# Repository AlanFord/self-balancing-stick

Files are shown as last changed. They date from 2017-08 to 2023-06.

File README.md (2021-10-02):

# self-balancing-stick
# UPDATE:
With apologies, this project was clearly beyond my skill set.  However, I've made a lot of progress and am closing in on completion.  Many thanks to a couple of makerspaces - [HackRVA](https://www.hackrva.org/blog/) and [BuildRVA](https://buildrva.spaces.nexudus.com/en).

The Countdown:
* 10 - Study control system theory so as to verify that replacement motors (torques, speeds, etc.) can still work. A lot has changed in this area since I last studied it 45 years ago. (**Complete**)
* 9 - Determine new control parameters using said control system theory and MATLAB (love/hate relationship right there) (**Complete**)
* 8 - Learn Arduino programming (**Complete**)
* 7 - Learn to use machine tools such that I can fabricate parts ((**Complete**)
* 6 - Pause to build a claw machine (because who doesn't want a claw machine to pick up candy and plushies?) (**Complete**)
* 5 - Make the motor clamps from ABS on an X-Carve CNC router at HackRVA (**Complete**)
* 4 - Make the balancing point from acetal on a Sherline lathe at BuildRVA (**Complete**)
* 3 - Make the gyro mount from HDPE on a Grizzly manual lathe at BuildRVA (**Complete**)
* 2 - Make the motor mount block from aluminum on a Tormach 1100 CNC mill at BuildRVA (**Complete**)
* 1 - Fabricate the reaction wheels (**In Progress!**)
* Go! (In the Near Future)

Dual Axis Reaction Wheel Inverted Pendulum

This project is inspired by an earlier project by Mike Rouleau.  For details, read [Mike.md](../master/Mike.md).

My design looks similar to Mike's, but a lot of the components required substitutes
* Motors (unavailable) replaced with Pololu brushed DC motors and hubs
* Rotors modified to mount on the hubs
* Control system parameters modified to reflect new motor constants
* Motor drivers modified to match the motors
* Unique Arduino shield designed to support two motor drivers and a connector
for the gyro

My CAD work is being done in Fusion 360.  I haven't added those files to this repository yet, but in some cases drawings (in the form of PDFs) have been included.

Design of the control system is being done in Matlab and documented in LaTeX.  The
work can be found in the folders (you guessed it) matlab and latex.

The hardware is based on what I have at hand.  
* The shaft is a 1 ft length of 3003 Aluminum tube (McMaster Carr part number 7237K33)
* 4.4:1 Metal Gearmotor 25Dx48L mm MP 12V with 48 CPR Encoder (Pololu Part # 3237)
* Pololu Universal Aluminum Mounting Hub for 4mm Shaft, #4-40 Holes (2-Pack) (Pololu Part # 1081)
* Adafruit 9-DOF Absolute Orientation IMU Fusion Breakout - BNO055 (Adafruit Part # 2472)
* Gy-521 MPU-6050 Module 3 Axis Analog Gyro and Accelerometer (various suppliers on Amazon)

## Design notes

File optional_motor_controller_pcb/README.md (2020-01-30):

# Arduino Shield for the Self-Balancing Stick

The Arduino firmware supports options for two different motor drivers - the Pololu Dual MAX14870 Motor Driver Shield (https://www.pololu.com/product/2519) and a custom shield that also uses the Maxim MAX14870 chips as motor drivers.

The Pololu motor driver shield was used in the initial testing stages to ensure the hardware and software worked together properly.  However, I found the Dupont headers to make a less-than-satisfactory connection when moving parts are involved.  Hence the move to a custom design.

The design for the Arduino shield is intended to include motor drivers for two dc motors as well as the interface for a GY-521 Gyro.

The motor drivers each use a MAX14780 motor driver IC. A barrel jack (2.1 mm, center-positive) on the shield provides power for the motors (12V, 4.2A max).  Separate pin headers are made available for connecting the motors and the GY-521 gyro.  The motors are Pololu 4.4:1 gear motors witha 48 CPR encoder, requireing a 6-pin connector.  The GY-521 interface also requires a 6-pin connector.

The Arduino pins used by each of the connectors are as follows:

GY-521 -> Arduino

* SCL -> A5/SCL
* SDA -> A4/SDA
* INT -> A3

Left Motor -> Arduino

* Vcc -> +5V
* PWM -> D7
* DIR -> D8
* Encoder_A -> D2 (Interrrupt 0)
* Encoder_B -> A2

Right Motor -> Arduino

* Vcc -> +5V
* PWM -> D12
* DIR -> D13
* Encoder_A -> D3 (Interrupt 1)
* Encoder_B -> D6

The shield contains LEDs for both motors that indicate the direction the motor is being driven.

* Red LED -> DIR=1 (Clockwise)
* Green LED -> DIR=0 (Counterclockwise)

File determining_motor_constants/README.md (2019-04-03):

# Motor Testing

## Motor Constant
Using a new/different small brushed DC motor can be aggravating.  Specs for the motor can be missing
or of questionable accuracy.  The goal here is to physically test the motors and generate any missing
motor data.

Motor testing is documented in the LaTeX report Appendices.  Normally a motor torque constant would be
measured by using the motor to drive a known load and measure the current.  In this instance an attempt to
construct a Prony Brake to use in testing the motor was unsuccessful.  Instead, a basic set of data (V, I, and rotation speed)
can be used to determine the motor constants.

The Arduino program rpm.ino is used to measure the encoder output from the motor and calculate a velocity.
The program uses the Encoder library by Paul Stoffregen (see https://www.pjrc.com/teensy/td_libs_Encoder.html).
It can be installed from the Arduino IDE (Tools -> Manage Libraries ...).  Apply a known voltage to the motor,
measure the current, and read the velocity (counts/sec) from the Arduino using the Arduino IDE serial monitor.
The encoder output must be converted from counts/sec to RPM using the encoder coefficient (counts/rev).

The folder rpm contains the Arduino program.  The spreadsheet motorConstant.xlsx is used for data
averaging when determining the average encoder output.  

## Motor/Gearbox Friction Measurement

The friction in the motor and gearbox under load was measured by varying the voltage while measuring
the current and shaft speed (using rpm.ino).  The spreadsheet motorResistance.xlsx shows the data
reduction to determine both the Coulomb and viscous friction constants.

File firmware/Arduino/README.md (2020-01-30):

# Software

This software is derived from Mike Rouleau's work and is designed for the Arduino IDE.  The following packages are required for compilation:

* I2CDevLib - see https://www.i2cdevlib.com
* PinChangeInt - see https://github.com/GreyGnome/PinChangeInt
* digitalWriteFast - see https://github.com/watterott/Arduino-Libs/tree/master/digitalWriteFast

Note that the PinChangeInt library isn't being updated and should be replaced.  DigitalWriteFast may no longer
be needed (digital writes appear to have been sped up).  I2CDevLib has several components that will be needed -
install the whole whopping thing or add parts to Arduino/library as you find you need them.

## Changes You Need to Make

There are a number of parameters in the code that may need to be altered,
depending on the hardware that you are using.  Identical changes would need to be made both in the main Controller_3.0 sketch and in the testing sketches:

* serial_Frequency (\_1_Global_Variables.ino) - The baud rate for serial communications with your computer
* encoder_PPR (\_1_Global_Variables.ino) - the number of encoder pulses per revolution of the reaction wheels.  This value is dependent on the encoder and the gearing (if any) of the motor.
* encoder_Tick_Resolution (\_1_Global_Variables.ino) - If you have a high PPR value, set this to something like 10 for noise reduction.
* gyro offsets (\_3_Setup.ino) - These will be specific to your gyro.  Specify the X Gyro Offset, the Y Gyro Offset, Z Gyro Offset, and the Z Acceleration Offset.  If you don't have these values, run the calibarateIMU sketch to measure them.
* Arduino pin definitions (main sketch file for each application) - These, located in the Controller_3.0.ino file, will depend on what motor driver you are using.  I've included to sets - chosen based on whether POLOLU or CUSTOM is defined (with a #define statement).
* Controller Feedback Variables (\_1_Global_Variables.ino) - These have names like "omega_Kp" and "theta_Kd".  They can be set via the serial link when the sketch is running, or they can be set in the global variables file.
* A Little Math (\_5_Functions.ino) - The comments at the top of the file indicate the relationship between motor orientation, motor voltage, motor shaft rotation direction, Theta, and Omega.  If your design doesn't have an identical set of relationships, use the testing sketches to determine how the relationships change.  If a positive Omega is associated with a negative ypr[1], change ypr[1] to -ypr[1] when calculating omega_Now_Unfiltered.  A similar change might be needed when calculating theta_Now_Unfiltered.  You may also need to look at \_5_Interrupts.ino to make sure the encoder directions are working correctly.

## Summary of Files:
* Controller_3.0.ino
	This is really just a dummy file intended to contain the library include files and 
	Arduino pin assignments.  The normal Arduino functions (setup and loop) are located elsewhere.

* \_1_Global_Variables.ino:
	Here we have a lot of #define statement used to define macros that will be used in the Arduino code.
	These are followed by other global variables and global volatile variables that may be changed while
	processing interrupts.

* \_3_Setup.ino:
	Here we have the traditional setup() function that would normally be found in the Controller_3.0.ino file.
	setup() includes a number of actions -
	* initializes the serial output
	* sets the pin modes for the IMU interrupt input and motor controler outputs
	* sets the pull up on the IMU interrupt pin
	* attaches functions to the IMU and encoder interrupts
	* sets the PWM wavelength (?)
	* initializes the IMU

* \_4_MainLoop.ino
	Here we have the traditional loop() function that would normally be found in the Controller_3.0.ino file.
	The loop() function is really just a container for a huge switch statement.  The switch variable (stat)
	is set from user input through the serial monitor.
```	
    Code 	Character	Function  
    127		Del 		Motors off, but print updates (?)
    121		y 		Charge left motor
    104		h 		Charge right motor
    110		n 		Charge both motors
    117		u 		Balance with left motor
    106		j 		Balance with right motor
    109		m		Balance with both motors
    122		z 		Change Zeros 
    Subcodes:
	122	z 		Set both zeros to current value	
	120	x		Set theta zeros to current value
	99	c       	Set omega zeros to current value
	111	o 		Manually set theta zero
	108	l 		Manually set omega zero

    113		q 		set theta Kp
    119		w 		set theta Ki
    101		e 		set theta Kd
    114		r 		set theta Ks
    111		o 		set theta Kt
    97		a 		set omega Kp
    115		s 		set omega Ki
    100		d 		set omega Kd
    102		f 		set omega Ks
    108		l 		set omega Kt
    116		t 		set left Target Voltage
    103		g 		set right Target Voltage
    49		1		set the angle average filter
    50		2 		set the theta zero filter
    51		3 		set the omega zero filter
    52		4 		set the angle smoothed filter
    57		9		set the friction value
    112		p 		show extended data
```

\_5_Functions.ino
	Here we have most of the basic functions.
	The functions are:
	
	get_IMU_values()
	get_left_Encoder_Speeds()
	get_right_Encoder_Speeds()
	set_left_Motor_Voltage()
	set_right_Motor_voltage()
	update_Value() (prints current and changed value to the console)
	get_Serial() (reads a new value from the console)

\_5_Interrupts.ino
	Timing is everything!  These are the functions called by the hardware interrupts.
	
	ISR_left_Encoder()
	ISR_right_Encoder()
	dmpDataReady() (processes the IMU interrupt)

\_6_Controllers.ino
	This where the magic happens!  These implement the negative feedback for control.
	They don't really "get" values, rather they are calculating updated voltages based
	on the angles and speeds.
	
	get_left_PID_Voltage_Value()
	get_right_PID_Voltage_Value()

MPU6050_6Axis_MotionApps20_mod_1.h

	MPU6050::dmpInitialize()
	MPU6050::dmpPacketAvailable()
	MPU6050::dmpGetAccel()
	MPU6050::dmpGetQuaternion()
	MPU6050::dmpGetGyro()
	MPU6050::dmpGetLinearAccel()
	MPU6050::dmpGetLinearAccelInWorld()
	MPU6050::dmpGetGravity()
	MPU6050::dmpGetEuler
	MPU6050::dmpGetYawPitchRoll()
	MPU6050::dmpProcessFIFOPacket()
	MPU6050::dmpReadAndProcessFIFOPacket()

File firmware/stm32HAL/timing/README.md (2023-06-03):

## Timing

A simple program to calculate the best I2C configuration parameters, given an I2C source clock frequency and a
required I2C speed (I2C_SPEED_FREQ_STANDARD, I2C_SPEED_FREQ_FAST,
or I2C_SPEED_FREQ_FAST_PLUS).

This code was derived from the STM32 Arduino module twi.c.

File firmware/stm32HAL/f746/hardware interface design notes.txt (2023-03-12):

The software must interface with the hardware to make all of the work together.

MCU pins used to communicate with the motors, encoders, and the imu can be determined
from the #define statements in "main.h".  While many pins are used to support peripherals
built into the NUCLEO board, the following pins are critical to this project:

Serial Port -
USART3:
	RX - Pin D8
	TX - Pin D9
	
IMU -
I2C1:
	SDA - Pin B9
	SCL - Pin B8 (Not B6!)
GPIO:
	Data Ready Interrupt - Pin F15
	
Right Motor -
TIMER1:
	PWM - Pin E9
GPIO:
	Direction - Pin E11
TIMER3:
	Encoder Channel 1 - Pin A6
	Encoder Channel 2 - Pin C7
	
Left Motor -
TIMER2:
	PWM - Pin A0
GPIO:
	Direction - Pin F14
TIMER4:
	Encoder Channel 1 - Pin D12
	Encoder Channel 2 - Pin D13
	
----------------------------------------------------
Motor and IMU Orientation

The following was extracted from the file "imu.cpp".  The sketch
represents a top-down look at the motor and imu layout.

// Discussion of IMU values and motor orientation
//
//   -----------------------------------
//   |         Left Motor/Hub          |
//   |                                 |
//   -----------------------------------
//                  |        IMU top,front      ------
//                  |         -----------       |    |
//                  |         |         |       |    |
//              --------      |  Gy-521 |       |    |
//              |      |      |         |       |    |
//              |      |      -----------       |    |
//              |      |                        |    |
//              |      |      ----------------  |    | Right Motor/Hub
//              --------      |              |  |    |
//                            |              |==|    |
//                            |              |  |    |
//                            ----------------  |    |
//                                              |    |
//                                              |    |
//                                              |    |
//                                              |    |
//                                              |    |
//                                              ------
//
//      ypr[ ] values for pitch and roll are as follows
//      Front Edge Pitch Down:  Negative Values of ypr[1]
//      Front Edge Pitch Up:    Positive Values of ypr[1]
//      Roll to the Right:      Positive Values of ypr[2]
//      Roll to the Left:       Negative Values of ypr[2]
//
//      Note that "forward" motor rotations, associated with positive voltages,
//      are alway counter-clockwise when viewed from the "shaft end", and
//      clockwise when viewed from the motor body end.
//
//      Hence,
//      Positive Right Motor rotation ==> counter-clockwise shaft spin => pitch up => positive voltage ==> positive Omega ==> positive ypr[1]
//      Positive Left Motor rotation ==> counter-clockwise shaft spin  => roll to the right => positive voltage ==> positive Theta ==> positive ypr[2]
///////////////////////////////////////////////////////////////////////////////////////////////////

------------------------------------------------------
Encoder Description

The Pololu website states that the 25D DC motors with gearboxes have an encoder with 48 counts per coil revolution.  
With a gearbox of 4.4:1, this results in 48*4.4 = 211.2 counts per shaft revolution.  This is based
on counting both the rising and falling edges of both the A and B outputs.  This is a suitable value to use
in this application because Timers 3 and 4 are configured in "TI1 and TI2" mode.

Important:  Voltage!
The Pololu encoders require a Vcc voltage of between 3.5V and 20V.  Hence, it is necessary that 
all of the encoder pins are 5V tolerant!
For the NUCLEO-F746ZG -
Function     Port/Pin        IC Pin  5V Tolerant?
L_ENC_CH1      D12             81       FT (Yes)
L_ENC_CH2      D13             82       FT (Yes)
R_ENC_CH1      A6              42       FT (Yes)
R_ENC_CH2      C7              97       FT (Yes)

------------------------------------------------------
Motor Driver Interface
Pololu Dual MAX14870 Motor Driver Shield for Arduino
https://www.pololu.com/product/2519
PWM operation up to 50 kHz
The required pins are:
DIR -> 0=forward at speed PWM %
       1=reverse at speed PWM %
PWM -> speed %

Timer Configuration:
Assume PCLK for each motor timer is 72MHz (check this for each change in MCU!!!)
Assume ARR = 255 (based on the controller code and motor voltage routines)
(PSC+1)*(ARR+1) = Fclk/Fpwm = ratio = 72MHz / 50 kHz = 1440
PSC = (ratio/(ARR+1)) -1 = (1440/256) -1 = 5.625, rounded to 6
Check:
Fpwm = Fclk/(ARR+1)/(PSC+1) = 72E6 / 256 / 7 = 40.1 kHz
______________________________________________________
IMU Interface
The IMU is a GY-521 board using a MPU-6050 module.
The required pins are:
VCC -> 3.3V/5V
GND -> GND
SCL -> B6
SDA -> B9
XDA ->
XCL ->
ADO ->
INT -> F15

The INT signal is an open-drain line that should be RISING when data is ready for download to the MCU.
The MPU-6050 can accommodate I2C frequencies of up to 400 kHz.  The original Arduino design
of this software used 100 kHz.
The I2C rise time was set at 500 nsec, based on an average value for Std (100 kHz) operation.
The I2C fall time was set to 150 nsec, based on an average value for Std (100 kHz) operation.

The GY-521 uses a 3.3V level for SCL and SDA signaling.  This is compatible with 
the STM32 NUCLEO line.

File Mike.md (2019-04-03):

## A Salute to Mike Rouleau
This project is inspired by Mike Rouleau's "Self Balancing Stick", altered so that all of the components can be fabricated at local makerspaces.  Links to descriptions of Mike Rouleau's work are:
- http://hackaday.com/2016/08/11/stick-balances-itself-with-reaction-wheels/
- https://www.youtube.com/watch?v=woCdjbsjbPg
- https://drive.google.com/file/d/0B9CxKhrEOT-3Z2Y2ajhiaWl6QU0/view
- https://drive.google.com/file/d/0B9CxKhrEOT-3ekE1MnRoT3Izdm8/view
- https://grabcad.com/library/self-balancing-stick-dual-axis-reaction-wheel-inverted-pendulum-1/details
- https://www.reddit.com/r/arduino/comments/3n0g8p/self_balancing_stick_dual_axis_reaction_wheel/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

Primary components used by Mike are:
- Mitsumi M25N-2 series Motor with a 334 PPR Encoder
- Arduino Uno Rev 3
- Seeed Studio 4A Motor Shield
- GY-521 Gyro (uses the MPU-6050 chip)

Some links to parts used by Mike:
- http://www.ebay.com/itm/171395060368?_trksid=p2060353.m1438.l2649&ssPageName=STRK%3AMEBIDX%3AIT
- http://www.mitsumi.co.jp/latest/Catalog/pdf/motorav_m25n_2_e.pdf
- http://www.ebay.com/itm/231284342156?_trksid=p2060353.m1438.l2649&ssPageName=STRK%3AMEBIDX%3AIT

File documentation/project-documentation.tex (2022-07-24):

% arara: pdflatex
% arara: nomencl
% arara: pdflatex

\documentclass[12pt,letterpaper]{article}
\usepackage{amsmath}
\usepackage[colorlinks]{hyperref} 
\usepackage[title,toc,page]{appendix}
\usepackage{graphicx}
\usepackage{caption}
\usepackage{listings}
\usepackage{titlesec}
\usepackage{todonotes}
\usepackage[intoc]{nomencl}

%% This code creates the groups
% -----------------------------------------
\usepackage{etoolbox}
\renewcommand\nomgroup[1]{%
  \item[\bfseries
  \ifstrequal{#1}{A}{Physics constants}{%
  \ifstrequal{#1}{B}{Transfer Functions}{%
  \ifstrequal{#1}{O}{Other symbols}{}}}%
]}
% -----------------------------------------

\makenomenclature

\renewcommand{\nomname}{List of Symbols}
\renewcommand{\nompreamble}{The following list describes several symbols that will be used later within the body of the document}

\newcommand{\sectionbreak}{\clearpage}

\begin{document}

\title{Oh, What a Bot!}
\author{HackRVA.org}
\date{}
\maketitle

\tableofcontents

\printnomenclature[0.5in]

\section{Introduction}
This article describes the development of a control system model for an reaction wheel pendulum, shown in Figure \ref{sketchOfPendulum}.  A reaction wheel pendulum is a variation of a simple pendulum, balanced upright, with rotating wheels
at the top in place of the pendulum bob. Each wheel is driven by a separate motor.  The pendulum is inherently unstable in the upright position - gravity will pull the pendulum over if it is not perfectly balanced.  Thus, a control system is needed to accelerate the reaction wheels, applying torques
as needed to the pendulum so as to keep it upright. The reaction wheels are mounted at right angles to each other, providing the ability to 
correct the alignment of the pendulum in any direction.

The pendulum physical structure includes a rod, an accelerometer, and two flywheels.  Each
flywheel is comprised of a motor mount, a DC brushed motor, and a reaction wheel.  The flywheel assemblies are mounted at
the top of the rod at right angles to each other and the rod.  The DC motors are wired to a motor controller and an Arduino.  The Arduino is also wired
to the accelerometer, which is located at the top of the rod.

\todo{needs a figure number}The basics of the pendulum control system is outlined in Figure \ref{fig.basicControlSystem}.  The system
can be controlled by adjusting the voltage.  An additional input F is included to describe random environmental forces that may affect the pendulum.  The random forces may result in the desired angle of the pendulum not being achieved.  More accurate control will result from feeding the resulting pendulum angle back into the control system so that the input voltage is continuously adjusted until the desired pendulum angle is achieved.  This is shown in Figure \ref{basicControl}.

In this case, however, the goal is for the pendulum to remain vertical with as little wobble as possible.
The real control comes into play when correcting for the stray forces on the system.  Hence, the control
system can be reformulated as shown in Figure \ref{fig.regulatorControlSystem}, commonly known as
a Regulator Problem.  This structure emphasizes the environmental forces as the primary input into the
system and that the feedback is primarily intended to compensate for those forces.\todo{Figure 3 is missing a feedback arrow}

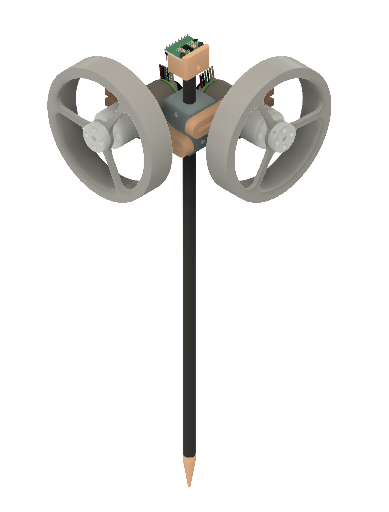
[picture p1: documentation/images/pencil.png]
 
    \captionof{figure}{Sketch of the Pendulum}  
    \label{sketchOfPendulum}
   

    \captionof{figure}{Simplified Pendulum Model}
    \label{basicControl}


    \captionof{figure}{Regulator Model}
    \label{fig.regulatorControlSystem}

\section{Pendulum Dynamics}

More detail can be added to the regulator control system description by building a mathematical model of the the
pendulum.
Figure \ref{modelOfPendulum} shows a simplified sketch of the inverted pendulum.
Reference \cite{reactionWheel} contains a summary of the model dynamics for the balancing pencil.  
The model dynamics can be summarized as
%
\begin{equation}
    m g l \sin \theta + F - I_{c}\ddot{\theta}  = I_{f}\ddot{\phi}
\end{equation}
%

\nomenclature[O]{\(m\)}{total mass of inverted pendulum (kg)}
\nomenclature[A]{\(g\)}{Gravitational constant (m s\textsuperscript{-2})}
\nomenclature[O]{\(l\)}{distance from the pivot point to the center of pendulum mass (m)}
\nomenclature[O]{\(\theta\)}{pendulum angle (rad)}
\nomenclature[O]{\(F\)}{environmental forces on the pendulum}
\nomenclature[O]{\(I_{c}\)}{moment of inertia of the pendulum (kg m\textsuperscript{2})}
\nomenclature[O]{\(I_{f}\)}{moment of inertia of the reaction wheel (kg m\textsuperscript{2})}
\nomenclature[O]{\(\phi\)}{flywheel angle (rad)}

Other references may have alternate formulations using different definitions for $\theta$ and $\phi$.\footnote{Reference \cite{monograph} has a slightly different formulation for the model dynamics; 
the sign of the gravitational term is positive rather than negative.  This difference is caused 
by Reference \cite{monograph} defining the angle from the downward, resting position
while Reference \cite{reactionWheel} defines the angle from the vertical.  
The cosines of angles differing by $\pi$ have opposite signs.}\\

After linearizing the equation by noting that $\sin{\theta} \approx \theta$ for small angles, 
the transfer function for the pendulum is then
%
\begin{equation}
    m \,g \,l \theta + F - I_{c}\ddot{\theta}  = I_{f}\ddot{\phi}
\end{equation}
%
The reaction wheel can be continuously revolving, making the reaction wheel angle $\phi$ less useful as a control parameter.
In its place we will use $\omega = \dot{\phi}$.
%
\begin{equation}
    m \,g \,l \theta + F - I_{c}\ddot{\theta}  = I_{f}\dot{\omega}\label{bigOne}
\end{equation}
%
For ease of use in later analysis, it is beneficial to split \eqref{bigOne} into two parts:
%
\begin{equation}
    m \,g \,l \theta + x(t)   = I_{c}\ddot{\theta}\label{eq.pendulum}
\end{equation}
%
\begin{equation}
    x(t) = F - I_{f}\dot{\omega}\label{eq.oddOne}
\end{equation}
%
\nomenclature[O]{\(x\)}{net torque applied to the pendulum (N m)}
where $x(t)$ is the net torque applied to the pendulum.  The sign convention is important; a positive torque $x(t)$
will accelerate the pendulum in the direction of the positive pendulum angle.  However, the sign convention in 
\eqref{eq.oddOne} indicates that  a positive acceleration of the rotor will result in a \textit{negative} acceleration of the pendulum.

Note that if the pendulum is not vertical (i.e. $\theta = 0$) gravity will begin to pull the pendulum over.  Correcting this requires accelerating the flywheel to apply torque to the pendulum.  A flywheel turning at a constant velocity applies no torque to the pendulum and will not alter the movement of the pendulum.

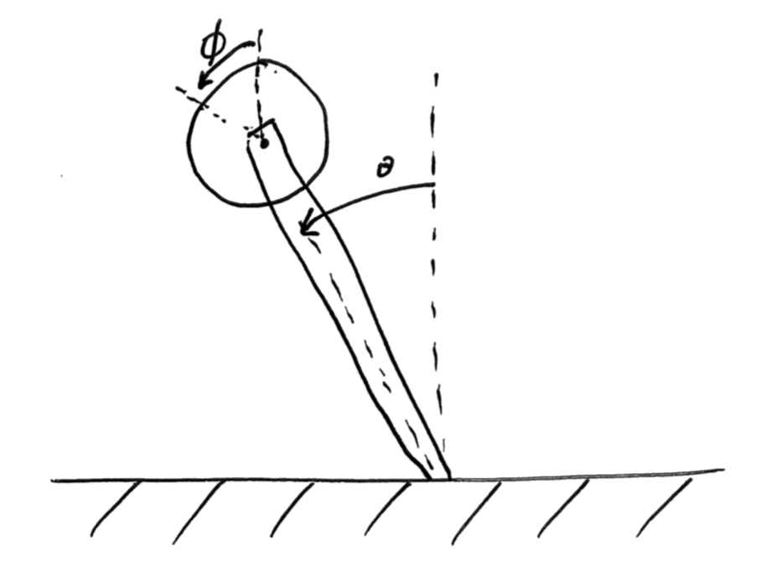
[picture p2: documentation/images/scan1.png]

    \captionof{figure}{Simplified Pendulum Model}
    \label{modelOfPendulum}

\section{Motor and Flywheel Dynamics}

Reference \cite{reactionWheel} models the motor as 
%
\begin{equation}
    I_{f} \, \ddot{\phi} \, \eta_{m} \, \eta_{g}  = K_{t} \, i
\end{equation}
%

\nomenclature[O]{\(\eta_{m}\)}{motor efficiency}
\nomenclature[O]{\(\eta_{g}\)}{gear efficiency}
\nomenclature[O]{\(K_{t}\)}{motor torque constant (N m A\textsuperscript{-1})}
\nomenclature[O]{\(i\)}{motor current (A)}

This formulation appears to have problems, as a reduction in the motor and gear efficiencies results in a 
greater flywheel acceleration for a given motor current.  Similarly, a gear ratio above unity would 
decrease the flywheel acceleration for a specified motor current/torque, which is non-physical.  The equation can be altered
to correct these issues, resulting in the following:
%
\begin{equation}
	I_{f} \, \ddot{\phi} = \, \eta_{m} \, \eta_{g} K_{t} \, i
\end{equation}
%
However, this format may not be the easiest to implement, as the motor and gear efficiencies are not known.  Reference \cite{monograph}
takes a different approach,\footnote{Note that there is no term in \eqref{simpleShaft} that represents torque associated
with external work done by the shaft.  Hence this formulation is limited to flywheels that are reasonably aerodynamic (e.g. not something that
acts as a propeller).}
%
\begin{equation}
    I_{f} \, \ddot{\phi} = T_{shaft}\label{simpleShaft}
\end{equation}
%
Where the earlier format dealt with motor/gear efficiencies using $\eta_{m}$ and $\eta_{g}$, Reference \cite{monograph} develops a correlation of friction in terms of torque required to maintain a given $\dot{\phi}$.  Here the torque will be
reformulated as 
%
\begin{equation}
    T_{shaft} = T - T_{friction}
\end{equation}
%
\begin{equation}
    T_{friction} = A \, sgn(\dot{\phi} - \dot{\theta} ) + B (\dot{\phi} - \dot{\theta})
\end{equation}
%
\begin{equation}
    T = K_{t} \, i
\end{equation}
%

\nomenclature[O]{\(T\)}{total motor torque (N m)}
\nomenclature[O]{\(T_{shaft}\)}{torque available to the flywheel (N m)}
\nomenclature[O]{\(T_{friction}\)}{torque lost to motor and gear friction (N m)}
\nomenclature[O]{\(A\)}{coulomb friction coefficient (N m)}
\nomenclature[O]{\(B\)}{rotational friction coefficient(N m rad\textsuperscript{-1} s)}

Note the use of $(\dot{\phi} - \dot{\theta})$.  Friction is dependent on the relative motion of the motor armature and the motor frame.  If the pendulum angular velocity $\dot{\phi}$ is equal to the reaction wheel angular velocity $\dot{\theta}$ there will be no relative motion between the motor armature and frame; no friction will occur.

Combining equations,
%
\begin{equation}
    I_{f} \, \ddot{\phi}  = K_{t} \, i - A \, sgn(\dot{\phi} - \dot{\theta} ) - B (\dot{\phi} - \dot{\theta})
\end{equation}
%
Again, using the notation $\omega = \dot{\phi}$,
%
\begin{equation}
    I_{f} \, \dot{\omega}  = K_{t} \, i - A \, sgn(\omega - \dot{\theta}) - B (\omega - \dot{\theta}) \label{wheel}
\end{equation}
%

As will be seen, this equation is easier to implement because $K_{t}$, $A$, and $B$ can be measured experimentally (see Appendix \ref{appendix:measure}).  

\section{Motor Control}
The previous chapter determined the relationship between the motor current and the acceleration of the flywheel.  
However, the motor will be not be controlled via motor current.  Instead, a motor controller will be used to control the 
motor by adjusting the motor voltage via a PWM signal.  The equivalent, average voltage will then regulate the motor.  
Following Reference \cite{monograph}, but recognizing the motor is at the end of a pendulum, the relationship between motor current and voltage is
%
\begin{equation}
    L\, \frac{di}{dt} + r \,i = v - K_{v} \, (\omega - \dot{\theta})
\end{equation}
%

\nomenclature[O]{\(L\)}{armature inductance (H)}
\nomenclature[O]{\(r\)}{armature resistance ($\Omega$)}
\nomenclature[O]{\(v\)}{voltage supplied to the motor (V) }
\nomenclature[O]{\(K_{v}\)}{motor voltage constant (V rad\textsuperscript{-1} s)}
\nomenclature[O]{\(\omega\)}{motor rotation speed (rad s\textsuperscript{-1})}

Normally the inductance of the motor is much lower than the resistance, such that $L/r \sim 0.001$ sec.  
In such cases it is acceptable to ignore the time dependence of the current and write
%
\begin{equation}
    r \,i = v - K_{v} \, (\omega - \dot{\theta}) \label{motor}
\end{equation}
%

Solving for i:
%
\begin{equation}
    i = \frac{v}{r} - \frac{K_{v} \, (\omega - \dot{\theta})}{r}
\end{equation}
%
Combining with \eqref{wheel}
%
\begin{equation}
    I_{f} \, \dot{\omega}  =  K_{t} \, \left( \frac{v}{r} - \frac{ K_{v} \, (\omega - \dot{\theta})}{r} \right) - A \, sgn(\omega - \dot{\theta} ) - B (\omega - \dot{\theta})
\end{equation}
Rearranging,

\begin{equation}
    I_{f} \, \dot{\omega} + \left( B+\frac{K_{t} K_{v}}{r} \right) (\omega - \dot{\theta}) +A \, sgn(\omega - \dot{\theta})= \left(\frac{K_{t}} {r}\right)v \label{eq.motorSemiFinal}
\end{equation}

Not all of the voltage results in acceleration of the reaction wheel.  As the reaction wheel velocity increases, an
increasing amount of the voltage (and the resulting torque) is consumed by friction and the back EMF.\\

The voltage used to drive the motor is determined by the controller.  Here the voltage will be set to the output of the controller
\begin{equation}
    v = u 
\end{equation}
\nomenclature[O]{\(u\)}{controller output}
Substituting into \eqref{eq.motorSemiFinal}
\begin{equation}
    I_{f} \, \dot{\omega} + \left( B+\frac{K_{v} K_{t}}{r} \right) (\omega - \dot{\theta}) +A \, sgn(\omega - \dot{\theta}) = \left(\frac{K_{t}} {r}\right)u\
\end{equation}
The simple substitution of $u$ for $v$ does not seem to have much purpose at this point in the analysis, but will be useful
when complex controllers are evaluated.\\

It is useful to assume that the control function can adjust the demand voltage by adding or subtracting a constant, depending on the current spin direction of the reaction wheel.  This means that $-A\,sgn(\dot{\phi})$ is folded
into $u$ for the purposes of this analysis.  Our motor control equation is then
\begin{equation}
    I_{f} \, \dot{\omega} + \left( B+\frac{K_{v} K_{v}}{r} \right) (\omega - \dot{\theta}) = \left(\frac{K_{t}} {r}\right)u\label{eq.motorFinal} 
\end{equation}

\section{Modeling in the Frequency Domain}
\label{sec:Modeling}

The primary objectives of a control system for the pendulum should be to stabilize the upright position of the pendulum and recovering from external forces on the pendulum.  In addition, the control system should be designed to deal with a number
of physical limitations of the physical components of the pendulum.  Specifically,
\begin{itemize}
    \item the motor voltage is limited to maximum value,
    \item the rotor velocity has a practical upper limit.
\end{itemize}

The stability of the system shown in Figure  \ref{fig.regulatorControlSystem} can be evaluated by examining the
open loop transfer function
\begin{equation}
    T(s) = P(s) C(s) M(s) R(s)
\end{equation}

\nomenclature[B]{\(P(s)\)}{pendulum transfer function}
\nomenclature[B]{\(C(s)\)}{control function}
\nomenclature[B]{\(M(s)\)}{motor transfer function}
\nomenclature[B]{\(R(s)\)}{rotor transfer function}
\nomenclature[B]{\(T(s)\)}{open loop transfer function}

The control system in terms of these transfer functions is shown in Figure \ref{transferFunction}.\\

The controller, at this point in the analysis, is assumed to be a pass-through, or
%
\begin{equation}
u = \theta
\end{equation}
Hence, the controller transfer function is
\begin{equation}
C(s) = \frac{u(s)}{\theta(s)} = 1
    \label{EQ.simpleController}
\end{equation}

The pendulum transfer function can be derived from \eqref{eq.pendulum}
%
\begin{equation}
    m \,g \,l \theta(s) + x(s) = I_{c}\theta(s) s^{2}
\end{equation}

Ignoring the environmental forces, the pendulum transfer function is 
\begin{equation}
    P(s) = \frac{\theta(s)}{x(s)}= \frac{1}{I_{c} s^{2} - m g l }
    \label{franco}
\end{equation}
%
The rotor transfer function can be derived from \eqref{eq.oddOne} by noting that the torque generated by the flywheel is
\begin{equation}
    x(s) = F(s) - I_{f}\omega(s) s
\end{equation}
%
\begin{equation}
    R(s) = \frac{x(s)}{\omega(s)} = -I_{f} s
    \label{groucho}
\end{equation}\\

Note that the transfer function for the rotor in \eqref{groucho} is negative.  Combined with the summing
junction shown in Figure \ref{transferFunction}, this produces a negative feedback control system.\\

The motor transfer function must be derived from \eqref{eq.motorFinal}.  However,  in \eqref{eq.motorFinal} $\omega$
is a function of both $\theta$ and $u$, preventing the determination of a single-input, single-output transfer function.  One solution is to make the approximation $\omega \approx (\omega - \dot{\theta})$.  The reaction wheel may rotate at hundreds of RPM, while the pendulum is expected to deviate from vertical for only brief periods.  With this approximation 
the motor transfer function can be derived from \eqref{eq.motorFinal} as
\begin{equation}
    I_{f} \, \omega(s) s + \left( B+\frac{K_{v} K_{t}}{r} \right) \omega(s) = \left(\frac{K_{t}} {r}\right)u(s)
\end{equation}
%
\begin{equation}
    M(s) = \frac{\omega(s)}{u(s)} =  \frac{\left(\frac{K_{t}} {r}\right)}{I_{f} s + (\frac{K_{v} K_{t}}{r}+B)}
    \label{rondo}
\end{equation} 

Using \eqref{EQ.simpleController}, \eqref{franco}, \eqref{groucho}, and \eqref{rondo} results in 
%
\begin{equation}
	T(s) =\frac{-(\frac{1} {I_{c}})(\frac{K_{t}}{r})s}
	{(s^2-\frac{m g l}{I_{c}})(s+(\frac{K_{v} K_{t}}{r I_{f}}+\frac{B}{I_{f}}))}
\end{equation}

Substituting in values from the appendixes, the transfer function for the pendulum is
\begin{equation}
	T(s) =\frac{-0.1731 s}{s^3 + 3.113 s^2 -34.8 s -108.3}
\end{equation}

The numerator of the transfer function is the characteristic equation that, when factored, is
$(s-5.899) (s+5.899) (s+3.113)$.

Using the root locus technique and the open loop transfer function, Figure \ref{rootLocus} shows the
behavior of the closed loop poles as a function of feedback gain.  Note that one pole is always in the right
half of the plane, indicating that the system is unstable regardless of the magnitude of the gain. \\

The system might be stabilized by using both proportional and derivative, or PD, feedback.  The control function would be:
\begin{equation}
	u = \theta + p\dot{\theta}
\end{equation}
thus
\begin{equation}
	C(s) = 1 + p s
\end{equation}
Rearranging,
\begin{equation}
	C(s) = p\left(s+\frac{1}{p}\right)\label{pd}
\end{equation}

indicating a zero at $1/p$ and a gain of $p$.
The results are sensitive to the placement of the zero.  Placing the zero to the right of the pole at -5.8993 
eliminates any oscillation but does not remediate the pole in the right half of the plane.  Placing the zero to the left of the pole at -5.8993 results in a much faster response but can result in oscillations (Figure \ref{rootLocusPD}).  Again, the pole in the right half of the plane is not remediated. \\

One additional possibility for resolving the issue of the zero at the origin would be to implement a PID controller.
\begin{equation*}
	u(t) = \theta(t) + q\int \theta\,dt + p\dot{\theta}
\end{equation*}
then
\begin{equation}
	C(s) = 1 + \frac{q}{s} + p s
\end{equation}
Rearranging,
\begin{equation}
	C(s) = p\left(\frac{s^2+\frac{s}{p}+\frac{q}{p}}{s}\right)
\end{equation}

This controller would have two zeros that can be placed as required and a pole that would cancel
the zero at the origin.  If the zeros are placed to the left of the pole at -4.7303, then the system may stabilize.
However, in the real world the original zero may not be exactly at the origin and the poles in the left side of the axis may not be exactly where they are expected (due to nonlinearities, etc.) 
leading to a less-than robust control system. \todo{verify this}\\

Finally, it is possible to include feedback from the other monitored and controlled variable, the rotor velocity.
Unfortunately, to continue to evaluate the system using a root locus analysis, the feedback from
the rotor velocity cannot be included directly in $C(s)$, as it would introduce a second input into the transfer function.  
Instead, the definition of the motor voltage $v$ is modified to include the effect of the rotor velocity feedback
\begin{equation}
    v = u + K_{\omega}\omega
\end{equation}
\nomenclature[O]{\(K_{\omega}\)}{rotor velocity feedback gain}

where $u$ continues to represent the output of a PID controller using $\theta$ as an input and $K_{\omega}\omega$ is an additional feedback
from the rotor velocity.
%
This results in \eqref{eq.motorFinal} transforming into
\begin{equation}
    I_{f} \, \dot{\omega} + \left( B+\frac{K_{v}^2}{r} \right) \omega +A \, sgn(\omega)= \left(\frac{K_{v}} {r}\right)(u + K_{\omega}\omega)
\end{equation}
The motor transfer function is then
\begin{equation}
    I_{f} \, \omega(s) s + \left( B+\frac{K_{v}^2}{r} \right) \omega(s) = \left(\frac{K_{v}} {r}\right)(u(s)+K_{\omega} \omega(s))
\end{equation}
Rearranging terms,
\begin{equation}
    M(s) = \frac{\omega(s)}{u(s)} =  \frac{\left(\frac{K_{v}} {I_{f}r}\right)}{s + (\frac{1}{I_{f}})(\frac{K_{v}^2}{r}-\frac{K_{v} K_{\omega}}{r}+B)}
    \label{rondoMucho}
\end{equation} 

Using \eqref{pd}, \eqref{franco}, \eqref{groucho}, and \eqref{rondoMucho}, the open loop transfer function is now
\begin{equation}
	T(s) =\frac{-(\frac{Kp} {I_{c}r})(s+\frac{1}{p})s}
	{s^3 + (\frac{B r-K K_{\omega}+K^2}{I_{f}r})s^2 - (\frac{m g l}{I_{c}})s - (\frac{Br-K K_{\omega}+K^2}{I_{f}r} - \frac{m g l}{I_{c}})}\label{eq.openLoop}
\end{equation}

Figure \ref{rootLocusFull} shows the root locus with $p = 1/4.5$ and $K_{\omega} = 0.075$.  With a controller gain\footnote{The gain given here is in addition to the system gain modeled in \eqref{eq.openLoop}. } of 370 the controlling close loop poles are at -11.3, -1.33, and -1.12.\\


    \captionof{figure}{Control System Modeled as Transfer Functions}
    \label{transferFunction}

 
    \captionof{figure}{Root Locus Plot With Proportional Feedback}  
    \label{rootLocus}

 
    \captionof{figure}{Root Locus Plot With PD Feedback}  
    \label{rootLocusPD}

 
    \captionof{figure}{Root Locus Plot With PD and Rotor Velocity Feedback}  
    \label{rootLocusFull}

\section{State Space Model}

A State Space model can be constructed from equations \eqref{eq.motorSemiFinal} and \eqref{bigOne}.  The
state space variables are $\omega$, $\theta$, and $\dot{\theta}$.  The state space model
is then
\begin{equation}
\dot{x_{m}} = A_{m} x + B_{m} v
\end{equation}
where $x_{m} = (\omega, \theta, \dot{\theta})^{T}$ and

\begin{equation}
A_{m} = 
\begin{bmatrix}
-\frac{B}{I_{f}}-\frac{K_{v} K{t}}{I_{f} r} & 0 & \frac{B}{I_{f}}+\frac{K_{v} K{t}}{I_{f} r}\\
0 & 0 & 1\\
\frac{B}{I_{c}}+\frac{K_{v} K{t}}{I_{c} r} & \frac{mgl}{I_{c}} & -\frac{B}{I_{c}}-\frac{K_{v} K{t}}{I_{c} r}
\end{bmatrix}
\end{equation}

\begin{equation}
B_{m} = 
\begin{bmatrix}
\frac{K_{t}}{I_{f} r} \\
0 \\
 -\frac{K_{t}}{I_{c} r}
\end{bmatrix}
\end{equation}

However, measured sensor data from motor encoder signals are proportional to the relative velocity of the 
reaction wheel, $\omega_{r} = \omega - \dot{\theta}$.  Changing the state space variables to $x = (\omega_{r}, \theta, \dot{\theta})^{T}$ is performed using a transformation matrix $x = P x_{m}$ where
\begin{equation}
 P = 
\begin{bmatrix}
1 & 0 & -1\\
0 & 1 & 0\\
0 & 0 & 1\\
\end{bmatrix}
\end{equation}

From Reference \cite{book} the new state space model is then
\begin{equation}
\dot{x} = A x + B v
\end{equation}
\begin{equation}
y = C x + D v
\end{equation}
where $x = (\omega_{r}, \theta, \dot{\theta})^{T}$,  $y=(\omega_{r},\theta)^{T}$

\begin{equation}
A = P A_{m} P^{-1}
\end{equation}

\begin{equation}
B = P B_{m}
\end{equation}

resulting in

\begin{equation}
A = 
\begin{bmatrix}
-\frac{B}{I_{f}}-\frac{B}{I_{c}}-\frac{K_{v} K{t}}{I_{f} r}-\frac{K_{v} K{t}}{I_{c} r}  & -\frac{mgl}{I_{c}} & 0 \\
0 & 0 & 1\\
\frac{B}{I_{c}}+\frac{K_{v} K{t}}{I_{c} r} & \frac{mgl}{I_{c}} & 0
\end{bmatrix}
\end{equation}

\begin{equation}
B = 
\begin{bmatrix}
\frac{K_{t}}{I_{f} r} + \frac{K_{t}}{I_{c} r}\\
0 \\
 -\frac{K_{t}}{I_{c} r}
\end{bmatrix}
\end{equation}

\begin{equation}
C = 
\begin{bmatrix}
1 & 0 & 0 \\
0 & 1 & 0 
\end{bmatrix}
\end{equation}

\begin{equation}
D = 
\begin{bmatrix}
0  \\
0 
\end{bmatrix}
\end{equation}

\section{Implementation Details}

In \autoref{sec:Modeling} the necessary constants for the control system were developed.  However those constants
need to be adjusted for the reaction wheel pendulum.

The constants developed in \autoref{sec:Modeling} took the form
\begin{equation}
	C(s) = G(1 + \frac{q}{s} + p s)
\end{equation}
where G is the controller gain, q is the integral constant, and p is the derivative constant.  However the software requires
constants in the form of 
\begin{itemize}
    \item the proportional coefficient $K_{p}$
    \item the integral coefficient $K_{i}$
    \item the derivative coefficient $K_{d}$
    \item the rotor velocity coefficient $K_{s}$
\end{itemize}

$K_{s}$ is simply $K_{\omega}$.  To generate the other required constants, the controller equation is first restructured as
\begin{equation}
	C(s) = G + \frac{Gq}{s} + Gps
\end{equation}
From this it can be seen that $K_{i} = Gq$ and $K_{d} = Gp$.  The proportional constant requires a little more work.
Recall from \eqref{eq.openLoop} the system has a gain of $Kp/I_{c}r$.  All of these terms, with the exception of $p$ are a inherent to the hardware; p
is the derivative constant. $K_{p}$ is then
\begin{equation}
K_{p} = \frac{G} {p}
\end{equation}

Another item to note in the control system implementation is that the feedback should be \textit{positive} as shown in Figure \ref{transferFunction}.  This reflects the fact that the rotor transfer function in \eqref{groucho} is negative.  This can also be seen in Figure \ref{modelOfPendulum}, where accelerating the rotor in the direction of positive $\theta$ results in a negative change in $\phi$.\\

Finally, units matter.  This documentation was created with SI units, eliminating the need to incorporate a multitude of conversion factors.  However, software is frequently constructed in more common units, for example rotor velocity in RPM, angles in degrees, and time in milliseconds or microseconds.  Hence numerical values developed in this document may need to
be converted to other units prior to use.

\begin{thebibliography}{99}
\bibitem{monograph} Block, D. J., Astrom, K. J., and Spong, M. W. (2007).  \emph{The Reaction Wheel Pendulum}. Morgan \& Claypool Publishers.
\bibitem{reactionWheel} \href{http://www.diva-portal.se/smash/get/diva2:916271/FULLTEXT01.pdf}{Ramm, A., and Sjostedt, M. (2015). Reaction wheel balanced robot, Design and Sensor Analysis of Inverted Pendulum Robot. Technical Report, KTH Royal Institute of Technology.}
\bibitem{balanceBot} \href{https://kth.diva-portal.org/smash/get/diva2:916184/FULLTEXT01.pdf}{Hellman, H. and Sunnerman, H, (2015).  Two-Wheeled Self-Balancing Robot. Technical report, KTH Royal Institute of Technology.}
\bibitem{twoWheeled} \href{http://geoffrey.chauveau.free.fr/pendulum/reports/final_report.pdf}{Chauveau, G., Chazal, D., Nakayama, D., Olsen, E., and Palm, S., (2005).  Controlling the Reaction Wheel Pendulum.}
\bibitem{hackaday} \href{https://hackaday.com/2016/08/11/stick-balances-itself-with-reaction-wheels/}{"Stick Balances Itself With Reaction Wheels" by Gerrit Coetzee}
\bibitem{book} \href{https://eng.libretexts.org/Bookshelves/Industrial_and_Systems_Engineering/Book%3A_Introduction_to_Control_Systems_(Iqbal)/08%3A_State_Variable_Models/8.04%3A_Linear_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}{Iqbal, Kamran (2020).  \emph{Introduction to Control Systems}.}
\end{thebibliography}

\begin{appendices}

\section{Motor and Gear Set Data}

Key to much of the work so far are the constants associated with the motor and gear set, $K_{t}$, $K_{v}$, $R$, and $L$.
The following work is based on a \href{https://www.pololu.com/product/3237}{Pololu  4.4:1 metal gear motor}.  

Pololu gives the following parameters for the 4.4:1 gear motor: \\
weight = 95g \\
gear ratio = 4.4:1 \\
No-load speed @ 12V = 1700 rpm (178 rad/sec)\\
No-load current @ 12V = 0.2 A \\
Stall current @ 12V = 2.1 A \\
Stall torque @ 12V (at the gearbox shaft) = 11 oz in (0.07768 Nm)\\
Encoder frequency = 211.2 counts/rev of gearbox shaft\footnote{The encoder has a frequency of 48 counts per revolution when counting both edges of both channels. With a gear ratio of 4.4:1, the encoder frequency relative to the shaft rotation is 48*4.4 counts/rev, or 211.2 counts per shaft revolution when counting both edges of both channels.}\\

A number of the motor constants can be calculated from the published Pololu parameters.  However, it
should  be noted that, for inexpensive motors, the actual motor parameters may vary from the 
published data.  In any event, the motor constants will be calculated here and then later compared
with measured data.\\

$K_{t}$ can be calculated directly from the stall current and torque: $K_{t}$ = 0.07768 Nm /  2.1 A = 
0.0370 Nm/A.  $K_{v}$ can be set equal to $K_{t}$, or 0.0370 Vs.\\

The motor winding resistance can be determined from the rated voltage and the stall current, as no back-EMF is occurring at stall
conditions.  Thus, $R$ = 12 V / 2.1 A = 5.7 ohms.\\

Motor wiring is effected via the provided 0.1"-pitch connector.
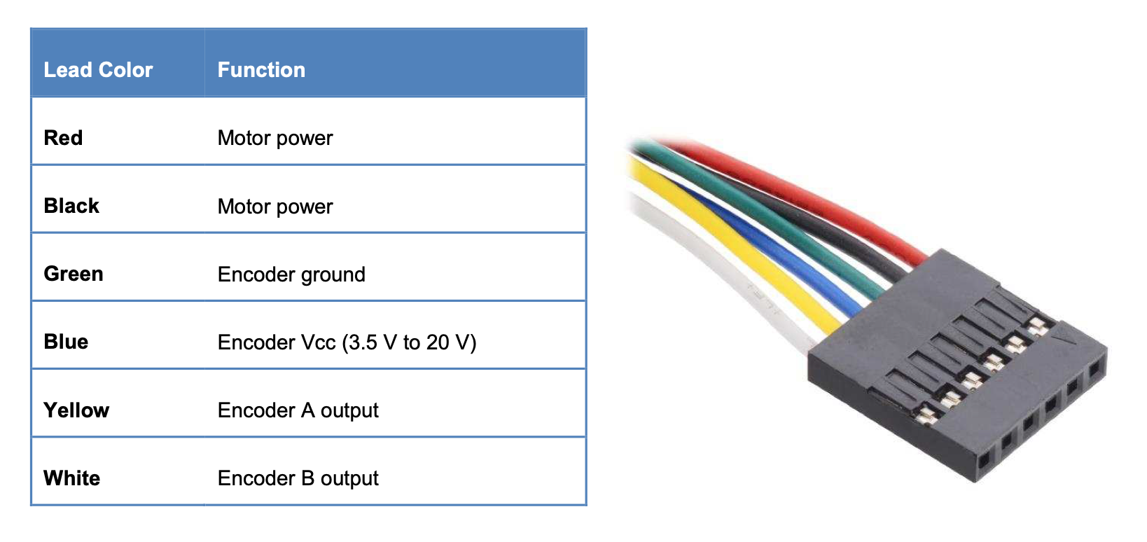
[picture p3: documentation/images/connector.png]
 

\section{Pendulum Constants}
A multitude of other values were calculated in MATLAB.\todo{needs values for both rotors and move after rotor description}  \\

\begin{tabular}{l l}
$m$ & 0.517327 kg \\
$l$ & 0.319038 m \\
$I_{c}$ & 0.046512 kg m\textsuperscript{2} \\
$I_{f}$ & 0.000168 kg m\textsuperscript{2} \\
$g$ & 9.81 m s\textsuperscript{-2} \\
\end{tabular}

\section{Measuring Motor Constants}
\label{appendix:measure}
Measurements were made to determine a number of motor constants, including $A$, $B$, $r$, $l$, and $K_{v}$, remembering that $K_{t} = K_{v}$ provided that SI units are used.\footnote{Provided SI units are used, $K_{v}$ and $K_{t}$ will have the same magnitude.  This can be seen by equating the 
mechanical and electrical power of a motor:
\begin{equation*}
    T \omega = v i
\end{equation*}
where $T$ is the motor torque.
Rearranging,
\begin{equation*}
    \frac{T}{i} = \frac{v}{\omega}
\end{equation*}
or
\begin{equation*}
    K_{t} = K_{v} 
\end{equation*}
}
Not all of these motor constants can be directly measured.  The resistance and inductance of the motor windings can be measured with an LCR meter.
Motor voltage, current, and RPM can be measured by connecting the motor to a power supply and varying the voltage.  The RPM can be measured either with a microcontroller monitoring the encoder or using a tachometer.\\

$\frac{A}{K_{t}}$ and $\frac{B}{K_{t}}$ can be determined from \eqref{wheel} by ensuring that the motor speed is constant.  Then
\begin{equation}
    i = \frac{A}{K_{t}}sgn(\omega) + \frac{B}{K_{t}} \omega
\end{equation}
Measuring $i$ at various values of $\omega$ permits estimating both $\frac{A}{K_{t}}$ and $\frac{B}{K_{t}}$ by linear
regression.  Optimally this should be performed using the rotor mounted on the motor. This ensures that
the weight of the rotor is accurately accounted for in the gearbox friction.\\

The next step is to determine values for $K_{v}$ (and hence $K_{t}$) and $R$.  Substituting \eqref{wheel} into \eqref{motor} and assuming a constant velocity we get
\begin{equation}
    v = r\frac{A}{K_{t}}sgn(\omega) + (r\frac{B}{K_{t}}+K_{v}) \omega
\end{equation}
Knowing $\frac{A}{K_{t}}$ and $\frac{B}{K_{t}}$ from the earlier regression, $r$ and $K_{v}$ can be determined by a linear regression of $v$ as a function of $\omega$.  Setting $K_{t}$ equal to $K_{v}$, values for $A$ and $B$ can then be resolved.\\

Measurements of $i$, $v$, and $\omega$ were performed with the motor driven by a 12 V power supply.  Current measurements were made with a  a $\mu$Current DVM adapter and voltage measurements were 
performed at the motor input leads.  Rotor angular velocity was measured with a hand-held tachometer.  The following table list the resulting measurements:

\begin{tabular}{|c|c|c|c|cl}
\hline
Case & $v$ & $i$ & $\omega$ & $\omega$ \\
      & (V) &  (A) & (RPM) & (rad/s) \\
\hline
1	& 0.0438	& 0.0034	& 0.	& 0. \\
2	& 0.286	& 0.015	& 0.	& 0. \\
3	& 0.601	& 0.0135	& 0.	& 0. \\
4	& 0.681	& 0.0788	& 0.	& 0. \\
5	& 1.02	& 0.0591	& 80.4	& 8.42 \\
6	& 1.487	& 0.0589	& 146.	& 15.29 \\
7	& 2.012	& 0.0599	& 230.	& 24.09 \\
8	& 2.532	& 0.0631	& 307.	& 32.15 \\
9	& 3.086	& 0.065	& 386.	& 40.42 \\
10	& 3.549	& 0.067	& 454.	& 47.54 \\
11	& 3.948	& 0.0682	& 511.	& 53.51 \\
12	& 4.56	& 0.0721	& 601.	& 62.94 \\
13	& 5.03	& 0.073	& 668.	& 69.95 \\
14	& 5.94	& 0.0751	& 807.	& 84.51 \\
15	& 6.84	& 0.0751	& 940.	& 98.44 \\
16	& 7.4	& 0.0765	& 1021.	& 106.92 \\
17	& 8.44	& 0.08	& 1175.	& 123.05 \\
18	& 9.46	& 0.082	& 1323.	& 138.54 \\
19	& 10.42	& 0.0839	& 1460.	& 152.89 \\
20	& 0.2618	& 0.0354	& 0.	& 0. \\
21	& 0.3561	& 0.0481	& 0.	& 0. \\
22	& 0.476	& 0.0646	& 0.	& 0. \\
23	& 0.597	& 0.0808	& 0.	& 0. \\
24	& 0.718	& 0.0969	& 0.	& 0. \\
25	& 0.722	& 0.0543	& 49.6	& 5.19 \\
\hline
\end{tabular}

 

 

Linear regression analysis results in the following values for the motor constants:\\
$A$ = 0.00363 N m\\
$B$ = 1.2E-5 N m/(radian/sec)\\
$r$ = 7.9 $\Omega$\\
$K_{v}$ = 0.0636 V sec\\

The coulomb friction represents approximately 5\% of the 
motor stall torque.  At the motor's no-load speed the viscous friction would double the total friction to 
approximately 7\% of the motor stall torque.  The viscous friction coefficient is significantly larger than
the value of 9.06E-7 N m/(radian/sec) measured in Reference \cite{twoWheeled}.  This may be due to
the gearbox associated with the motor used in the current work.  In any event, the friction will be included
in the system modeling.\\

$l$ was 
measured with the same instrument as 6.004 mH at 1kHz.  This gives a motor electrical time constant $l/r$ of 7.6E-4 sec.  This is the time taken by the current in the motor to go from rest to 63\% of the final steady-state current.  This
validates the assumption used in  \eqref{motor} .\\

\section{Arduino Code for Measuring RPM}

The following is an Arduino sketch can be used to monitor the speed of a dc motor in lieu of a tachometer.  The sketch is designed
to work with either an Arduino Uno or an Arduino Mega. The motor wiring described in the comments
referrs to the wiring of the Pololu 25D 4.4:1 metal gear motor.  The output is in position change 
per second, where the motor has 211.2 counts/rev of gearbox shaft. \\

\lstinputlisting{../determining_motor_constants/rpm/rpm.ino}

\section{Reaction Wheel Design Options}

The initial reaction wheel design was modeled after Reference \cite{hackaday}, with modifications to allow the reaction wheel
to mate properly with a Pololu motor hub.  The reaction wheel is shown in Figure \ref{reactionWheel}.
The reaction wheel body is Aluminum 6061 with an outer diameter of 90 mm, a width of 18 mm, and an annular thickness of 7 mm. 
Fusion 360 reports the mass of the reaction wheel to be 0.09391 kg (assuming a density of 2.7 g/cc).
The moment of inertia around the centerline is 1.562E-4 kg m\textsuperscript{2}.

An alternate, simpler design (although less elegant) is shown in Figure \ref{simpleReactionWheel}.
Fashioned from carbon steel with a density of  7.85 g/cc, the diameter of the wheel is 90 mm and the
thickness is 3.175 mm (1/8").  The reaction wheel mass is 0.175 kg and the moment of inertia 
around the centerline is 1.605E-04 kg m\textsuperscript{2}.  The simpler design with only a small change in the moment
of inertia permits an easier fabrication at a cost of a doubling of the reaction wheel mass.

A third, and final, design is less elegant still.  Figure \ref{acrylicReactionWheel} shows a reaction wheel fabricated from 3mm thick acrylic sheet, M6 button head bolts and nyloc nuts.  This design in intended to maintain a moment of inertia similar to the earlier designs, minimize the weight of the reaction wheel, and be easier to fabricate with common makerspace tools.  The wheel has an outer diameter of 90 mm with 12 bolts uniformly spaced at a radial distance of 39 mm.  The reaction wheel mass (including bolts) is  0.0808 kg, approximately half the mass of the steel reaction wheel.  The moment of inertial around the centerline (including the bolts) is 9.836E-05 kg m\textsuperscript{2}.  As with the other designs this reaction wheel is capable of being mated with a Pololu motor hub.

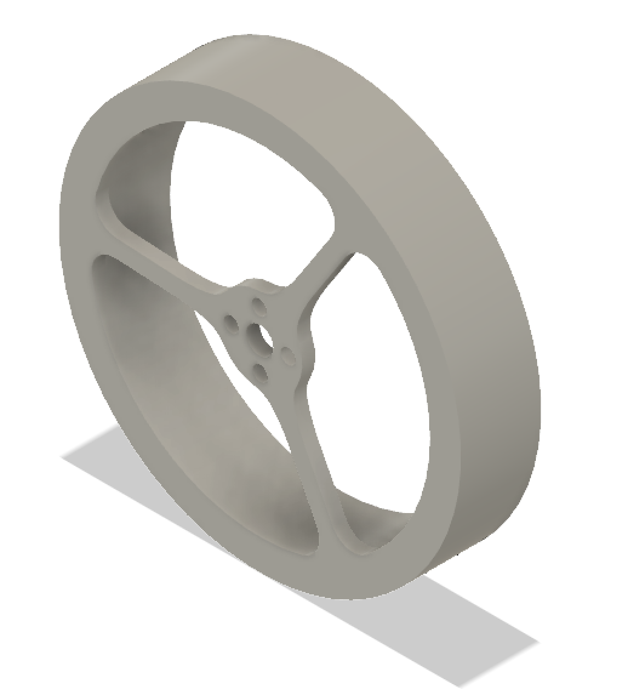
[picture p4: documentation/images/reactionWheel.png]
 
    \captionof{figure}{Aluminum Reaction Wheel}  
    \label{reactionWheel}

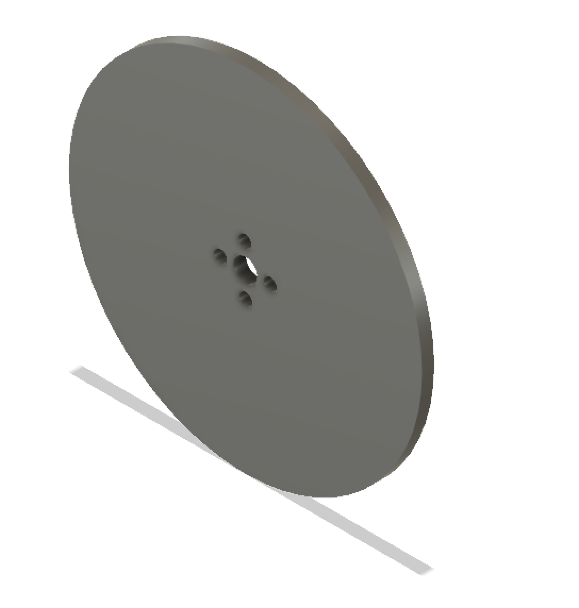
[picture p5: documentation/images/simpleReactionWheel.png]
 
    \captionof{figure}{Simplified Carbon Steel Reaction Wheel}  
    \label{simpleReactionWheel}

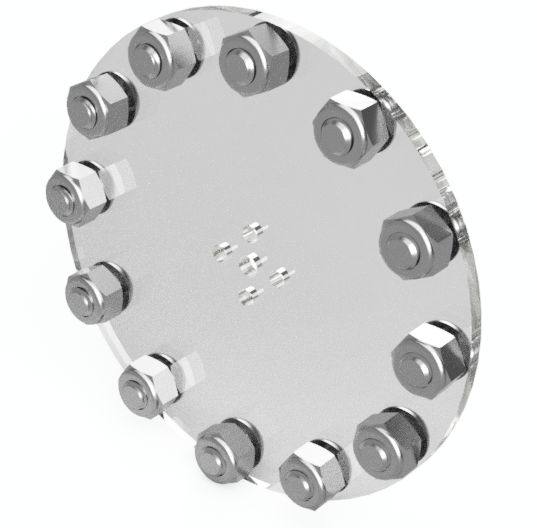
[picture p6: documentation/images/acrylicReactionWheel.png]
 
    \captionof{figure}{Simplified Acrylic Reaction Wheel}  
    \label{acrylicReactionWheel}

\end{appendices}

\end{document}

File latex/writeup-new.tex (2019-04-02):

\documentclass[12pt,letterpaper]{article}
\usepackage{amsmath}
\usepackage[colorlinks]{hyperref} 
\usepackage[title,toc,page]{appendix}
\usepackage{graphicx}
\usepackage{caption}
\usepackage{listings}
\usepackage{titlesec}
\newcommand{\sectionbreak}{\clearpage}
\begin{document}

\title{Oh, What a Bot!}
\author{HackRVA.org}
\date{}
\maketitle

\section{Introduction}
This article describes the development of a control system model for an reaction wheel pendulum, shown in Figure \ref{sketchOfPendulum}.  A reaction wheel pendulum is a variation of a simple pendulum, balanced upright, with rotating wheels
at the top in place of the pendulum bob. Each wheel is driven by a separate motor.The pendulum is inherently unstable in the upright position - gravity will pull the pendulum over if it is not perfectly balanced.  Thus, a control system is needed to accelerate the reaction wheels, applying torques
as needed to the pendulum so as to keep it upright. The reaction wheels are mounted at right angles to each other, providing the ability to 
correct the alignment of the pendulum in any direction.

The pendulum physical structure includes a rod, an accelerometer, and two flywheels.  Each
flywheel is comprised of a motor mount, a DC brushed motor, and a reaction wheel.  The flywheel assemblies are mounted at
the top of the rod at right angles to each other and the rod.  The DC motors are wired to a motor controller and an Arduino.  The Arduino is also wired
to the accelerometer, which is located at the top of the rod.

The basics of the pendulum control system is outlined in Figure \ref{fig.basicControlSystem}.  The system
can be controlled by adjusting the voltage.  An additional input F is included to describe random environmental forces that may affect the pendulum.  The random forces may result in the desired angle of the pendulum not being achieved.  More accurate control will result from feeding the resulting pendulum angle back into the control system so that the input voltage is continuously adjusted until the desired pendulum angle is achieved.  This is shown in Figure \ref{basicControl}.

In this case, however, the goal is for the pendulum to remain vertical with as little wobble as possible.
The real control comes into play when correcting for the stray forces on the system.  Hence, the control
system can be reformulated as shown in Figure \ref{fig.regulatorControlSystem}, commonly known as
a Regulator Problem.  This structure emphasizes the environmental forces as the primary input into the
system and that the feedback is primarily intended to compensate for those forces.

 
    \captionof{figure}{Sketch of the Pendulum}  
    \label{sketchOfPendulum}
   

    \captionof{figure}{Simplified Pendulum Model}
    \label{basicControl}


    \captionof{figure}{Regulator Model}
    \label{fig.regulatorControlSystem}

\section{Pendulum Dynamics}

More detail can be added to the regulator control system description by building a mathematical model of the the
pendulum.
Figure \ref{modelOfPendulum} shows a simplified sketch of the inverted pendulum.
Reference \cite{reactionWheel} contains a summary of the model dynamics for the balancing pencil.  
The model dynamics can be summarized as
%
\begin{equation}
    m g l \sin \theta + F - I_{c}\ddot{\theta}  = I_{f}\ddot{\phi}
\end{equation}
%
where: \\
$ m =$ total mass of inverted pendulum (kg)\\
$g =$ gravitational constant  (m s\textsuperscript{-2}) \\
$l =$ distance from the pivot point to the center of pendulum mass (m)\\
$\theta =$ pendulum angle (rad) \\
$F =$ environmental forces on the pendulum\\
$I_{c} =$ moment of inertia of the pendulum (kg m\textsuperscript{2}) \\
$I_{f} =$ moment of inertia of the reaction wheel (kg m\textsuperscript{2}) \\
$\phi =$ flywheel angle (rad) \\

Other references may have alternate formulations using different definitions for $\theta$ and $\phi$.\footnote{Reference \cite{monograph} has a slightly different formulation for the model dynamics; 
the sign of the gravitational term is positive rather than negative.  This difference is caused 
by Reference \cite{monograph} defining the angle from the downward, resting position
while Reference \cite{reactionWheel} defines the angle from the vertical.  
The cosines of angles differing by $\pi$ have opposite signs.}\\

After linearizing the equation by noting that $\sin{\theta} \approx \theta$ for small angles, 
the transfer function for the pendulum is then
%
\begin{equation}
    m \,g \,l \theta + F - I_{c}\ddot{\theta}  = I_{f}\ddot{\phi}
\end{equation}
%
The reaction wheel can be continuously revolving, making the reaction wheel angle, $\phi$, less useful as a control parameter.
In its place we will use $\omega = \dot{\phi}$.
%
\begin{equation}
    m \,g \,l \theta + F - I_{c}\ddot{\theta}  = I_{f}\dot{\omega}\label{bigOne}
\end{equation}
%
For ease of use in later analysis, it is beneficial to split \eqref{bigOne} into two parts:
%
\begin{equation}
    m \,g \,l \theta + u(t)   = I_{c}\ddot{\theta}\label{eq.pendulum}
\end{equation}
%
\begin{equation}
    u(t) = F - I_{f}\dot{\omega}\label{oddOne}
\end{equation}
%
where $u(t)$ is the net torque applied to the pendulum.  The sign convention is important; a positive torque $u(t)$
will accelerate the pendulum in the direction of the positive pendulum angle.  However the sign convention in 
\eqref{oddOne} indicates that  a positive acceleration of the rotor will result in a \textit{negative} acceleration of the pendulum.

Note that if the pendulum is not vertical (i.e. $\theta = 0$) gravity will begin to pull the pendulum over.  Correcting this requires accelerating the flywheel to apply torque to the pendulum.  A flywheel turning at a constant velocity applies no torque to the pendulum and will not alter the movement of the pendulum.


    \captionof{figure}{Simplified Pendulum Model}
    \label{modelOfPendulum}

\section{Motor and Flywheel Dynamics}

Reference \cite{reactionWheel} models the motor as 
%
\begin{equation}
    I_{f} \, \ddot{\phi} \, \eta_{m} \, \eta_{g}  = K_{t} \, i
\end{equation}
%
where: \\
$\eta_{m} =$ motor efficiency \\
$\eta_{g} =$ gear efficiency \\
$K_{t} =$ motor torque constant (N m A\textsuperscript{-1}) \\
$i =$ motor current \\

This formulation appears to have problems, as a reduction in the motor and gear efficiencies results in a 
greater flywheel acceleration for a given motor current.  Similarly, the gear ratio above unity would 
decrease the flywheel acceleration for a specified motor current/torque, which is non-physical.  The equation can be altered
to correct these issues, resulting in the following:
%
\begin{equation}
	I_{f} \, \ddot{\phi} = \, \eta_{m} \, \eta_{g} K_{t} \, i
\end{equation}
%
However, this format may not be the easiest to implement, as the motor and gear efficiencies are not known.  Reference \cite{monograph}
takes a different approach,
%
\begin{equation}
    I_{f} \, \ddot{\phi} = T_{shaft}
\end{equation}
%
Where the earlier format dealt with motor/gear efficiencies using $\eta_{m}$ and $\eta_{g}$, Reference \cite{monograph} develops a correlation of friction in terms of torque required to maintain a given $\dot{\phi}$.  Here the torque will be
reformulated as 
%
\begin{equation}
    T_{shaft} = T - T_{friction}
\end{equation}
%
\begin{equation}
    T_{friction} = A \, sgn(\dot{\phi} ) + B \dot{\phi} 
\end{equation}
%
\begin{equation}
    T = K_{t} \, i
\end{equation}
%
where \\
$T =$ the total motor torque \\
$T_{shaft} =$ torque available to the flywheel \\
$T_{friction} =$ torque lost to motor and gear friction \\
$A =$ coulomb friction coefficient \\
$B =$ rotational friction coefficient \\

Combining equations and adding the reduction gear ratio,
%
\begin{equation}
    I_{f} \, \ddot{\phi}  = K_{t} \, i - A \, sgn(\dot{\phi} ) - B \dot{\phi}
\end{equation}
%
Again, using the notation $\omega = \dot{\phi}$,
%
\begin{equation}
    I_{f} \, \dot{\omega}  = K_{t} \, i - A \, sgn(\omega) - B \omega \label{wheel}
\end{equation}
%

As will be seen, this equation is easier to implement because $K_{t}$, $A$, and $B$ can be measured experimentally (see Appendixes \ref{appendix:measure} and \ref{appendix:friction}).

\section{Motor Control}
The previous chapter determined the relationship between the motor current and the acceleration of the flywheel.  
However, the motor will be not be controlled via motor current.  Instead, a motor controller will be used to control the 
motor by adjusting the motor voltage via a PWM signal.  The equivalent, average voltage will then regulate the motor.  
Reference \cite{monograph} give the relationship between motor current and voltage as
%
\begin{equation}
    l \, \frac{di}{dt} + r \,i = v - K_{v} \, \omega
\end{equation}
%
where: \\
$l =$ armature inductance (henry) \\
$r =$ armature resistance (ohm) \\
$v =$ voltage supplied to the motor (volt) \\
$K_{v} =$ motor voltage constant (V  rad\textsuperscript{-1} sec) \\
$\omega =$ motor rotation speed (rad sec\textsuperscript{-1}) \\

Normally the inductance of the motor is much lower than the resistance, such that $l/r \sim 0.001$.  
In such cases it is acceptable to ignore the time dependence of the current and write
%
\begin{equation}
    r \,i = v - K_{v} \, \omega \label{motor}
\end{equation}
%
Note that, provided mks units are used, $K_{v}$ and $K_{t}$ will have the same magnitude.  This can be seen by equating the 
mechanical and electrical power
%
\begin{equation}
    T \omega = v i
\end{equation}
%
where $T =$ is the motor torque.
Rearranging,
%
\begin{equation}
    \frac{T}{i} = \frac{v}{\omega}
\end{equation}
%
or
%
\begin{equation}
    K_{t} = K_{v} 
\end{equation}
%

Back to the motor equation, we can solve \eqref{motor} for i:
%
\begin{equation}
    i = \frac{v}{r} - \frac{K_{v} \, \omega}{r}
\end{equation}
%
Combining with \eqref{wheel}
%
\begin{equation}
    I_{f} \, \dot{\omega}  =  K_{t} \, \left( \frac{v}{r} - \frac{ K_{v} \, \omega}{R} \right) - A \, sgn(\omega ) - B \omega
\end{equation}
Rearranging,

\begin{equation}
    I_{f} \, \dot{\omega} + \left( B+\frac{K_{t} K_{v}}{r} \right) \omega +A \, sgn(\omega)= \left(\frac{K_{t}} {r}\right)v 
\end{equation}

Recognizing that $K_{t} = K_{v}$ and replacing them with $K$,
\begin{equation}
    I_{f} \, \dot{\omega} + \left( B+\frac{K^2}{r} \right) \omega +A \, sgn(\omega)= \left(\frac{K} {r}\right)v\label{eq.motorFinal} 
\end{equation}

Not all of the voltage results in acceleration of the reaction wheel.  As the reaction wheel velocity increases, an
increasing amount of the voltage (and the resulting torque) is consumed by friction and the back EMF.

We will assume that the control function can adjust the demand voltage by adding or subtracting a constant, depending on the current spin direction of the reaction wheel.  This means that $-A\,sgn(\dot{\phi})$ is folded
into $v$ for the purposes of this analysis.  

\section{Modeling in the Frequency Domain}

The primary objectives of a control system for the pendulum should be to stabilize the upright position of the pendulum and recovering from external forces on the pendulum.  In addition, the control system should be design to deal with a number
of physical limitations of the physical components of the pendulum.  Specifically,
\begin{itemize}
    \item the motor voltage is limited to maximum value,
    \item The rotor velocity has a practical upper limit.
\end{itemize}

The stability of the system shown in Figure  \ref{fig.regulatorControlSystem} can be evaluated by examining the
open loop transfer function
\begin{equation}
    T(s) = P(s) C(s) M(s) R(s)
\end{equation}
where $P(s)$ is the pendulum transfer function, $C(s)$ is the control function, $M(s)$ is the motor transfer function, and $R(s)$ is the rotor transfer function.  
The control system in terms of these transfer functions is shown in Figure \ref{transferFunction}.\\

The controller, at this point in the analysis, is assumed to be a pass-through, or
%
\begin{equation}
v = \theta
\end{equation}
Hence, the controller transfer function is
\begin{equation}
C(s) = \frac{v(s)}{\theta(s)} = 1
    \label{EQ.simpleController}
\end{equation}

The pendulum transfer function can be derived from \eqref{eq.pendulum}
%
\begin{equation}
    m \,g \,l \theta(s) + u(s) = I_{c}\theta(s) s^{2}
\end{equation}

The rotor transfer function can be derived by noting that the torque generated by the flywheel is
\begin{equation}
    u(s) = F(s) - I_{f}\omega(s) s
\end{equation}
%
Ignoring the environmental forces, the pendulum transfer functions are 
\begin{equation}
    P(s) = \frac{\theta(s)}{u(s)}= \frac{1}{I_{c} s^{2} - m g l }
    \label{franco}
\end{equation}
%
\begin{equation}
    R(s) = \frac{u(s)}{\omega(s)} = -I_{f} s
    \label{groucho}
\end{equation}\\

Note that the transfer function for the rotor in \eqref{groucho} is negative.  Combined with the summing
junction shown in Figure \ref{transferFunction}, this produces a negative feedback control system.\\

From \eqref{eq.motorFinal} the transfer function for the motor is:
\begin{equation}
    I_{f} \, \omega(s) s + \left( B+\frac{K^2}{r} \right) \omega(s) = \left(\frac{K} {r}\right)v(s)
\end{equation}
\begin{equation}
    M(s) = \frac{\omega(s)}{v(s)} =  \frac{\left(\frac{K} {r}\right)}{I_{f} s + (\frac{K^2}{r}+B)}
    \label{rondo}
\end{equation} 

Using \eqref{EQ.simpleController}, \eqref{franco}, \eqref{groucho}, and \eqref{rondo} results in 
%
\begin{equation}
	T(s) =\frac{-(\frac{1} {I_{f}I_{c}})(\frac{K}{r})s}
	{(s^2-\frac{m g l}{I_{c}})(s+(\frac{K^2}{r I_{f}}+\frac{B}{I_{f}}))}
\end{equation}

Substituting in values from the appendixes, the transfer function for the pendulum is
\begin{equation}
	T(s) =\frac{-0.2464 s}{s^3 + 4.73 s^2 -34.8 s -164.6}
\end{equation}

The numerator of the transfer function is the characteristic equation that, when factored, is
$(s-5.8993) (s+5.8993) (s+4.7303)$.

Using the root locus technique and the open loop transfer function, Figure \ref{rootLocus} shows the
behavior of the closed loop poles as a function of feedback gain.  Note that one pole is always in the right
half of the plane, indicating that the system is unstable regardless of the magnitude of the gain.

One possible method of stabilizing the system would be to use both proportional and derivative, or PD, feedback.  The control function would be.
\begin{equation}
	C(s) = 1 + p s
\end{equation}
Rearranging,
\begin{equation}
	C(s) = \frac{s+\frac{1}{p}}{p}
\end{equation}

indicating a zero at $1/p$ and a gain of $1/p$.
The results are sensitive to the placement of the zero.  Placing the zero to the right of the pole at -5.8993 
eliminates any oscillation, but does not remediate the pole in the right half of the plane.  Placing the zero to the left of the pole at -5.8993 results in a much faster response, but can result in oscillations (Figure \ref{rootLocusPD}).  Again, the pole in the right half of the plane is not remediated. \\

One possibility for resolving the issue of the zero at the origin would be to implement a PID controller.
\begin{equation}
	C(s) = 1 + \frac{q}{s} + p s
\end{equation}
Rearranging,
\begin{equation}
	C(s) = \frac{ps^2+s+q}{s}
\end{equation}

This controller would have two zeros that can be placed as required and a pole that would cancel
the zero at the origin.  If the zeros are placed to the left of the pole at -4.7303, then the system may stabilize.
However, in the real world the original zero may not be exactly at the origin and the poles in the left side of the axis may not be exactly where they are expected (due to nonlinearities, etc.) 
leading to a less-than robust control system. \\

Finally, it is possible to include feedback from the other monitored and controlled variable, the rotor velocity.
Unfortunately, to continue to evaluate the system using a root locus analysis, the feedback from
the rotor velocity will have to be directly factored into the transfer function.  \\

Here we modify \eqref{motor} to include the feedback from the rotor velocity:
\begin{equation}
    r \,i = v +K_{\omega}\omega - K_{v} \, \omega \label{motorUpdated}
\end{equation}

where: \\
$ K_{\omega} =$ rotor velocity feedback gain.\\

Solving for i,
\begin{equation}
    i = \frac{v}{r} - \frac{(K-K_{\omega}) \, \omega}{r}
\end{equation}

and
\begin{equation}
    M(s) = \frac{\omega(s)}{v(s)} =  \frac{\left(\frac{K} {I_{f}r}\right)}{s + (\frac{1}{I_{f}})(\frac{K^2}{r}-\frac{K K_{\omega}}{r}+B)}
    \label{rondoMucho}
\end{equation} 

Using \eqref{EQ.simpleController}, \eqref{franco}, \eqref{groucho}, and \eqref{rondoMucho}, the open loop transfer function is now
\begin{equation}
	T(s) =\frac{-(\frac{K} {I_{c}r})s}
	{s^3 + (\frac{B r-K K_{\omega}+K^2}{I_{f}r})s^2 - (\frac{m g l}{I_{c}})s - (\frac{Br-K K_{\omega}+K^2}{I_{f}r} - \frac{m g l}{I_{c}})}
\end{equation}

Figure \ref{rootLocusFull} shows the root locus with $p = 1/4.5$ and $K_{\omega} = 0.075$.  With a system gain of 266 the controlling poles are at -11.5205, -1.5353, and -0.999.\\


    \captionof{figure}{Control System Modeled as Transfer Functions}
    \label{transferFunction}

 
    \captionof{figure}{Root Locus Plot With Proportional Feedback}  
    \label{rootLocus}

 
    \captionof{figure}{Root Locus Plot With PD Feedback}  
    \label{rootLocusPD}

 
    \captionof{figure}{Root Locus Plot With PD and Rotor Velocity Feedback}  
    \label{rootLocusFull}

\begin{thebibliography}{99}
\bibitem{monograph} Block, D. J., Astrom, K. J., and Spong, M. W. (2007).  \emph{The Reaction Wheel Pendulum} . Morgan \& Claypool Publishers.
\bibitem{reactionWheel} \href{http://www.diva-portal.se/smash/get/diva2:916271/FULLTEXT01.pdf}{Ramm, A., and Sjostedt, M. (2015). Reaction wheel balanced robot, Design and Sensor Analysis of Inverted Pendulum Robot. Technical Report, KTH Royal Institute of Technology.}
\bibitem{balanceBot} \href{https://kth.diva-portal.org/smash/get/diva2:916184/FULLTEXT01.pdf}{Hellman, H. and Sunnerman, H, (2015).  Two-Wheeled Self-Balancing Robot. Technical report, KTH Royal Institute of Technology.}
\bibitem{twoWheeled} \href{http://geoffrey.chauveau.free.fr/pendulum/reports/final_report.pdf}{Chauveau, G., Chazal, D., Nakayama, D., Olsen, E., and Palm, S., (2005).  Controlling the Reaction Wheel Pendulum.}
\end{thebibliography}

\begin{appendices}

\section{Motor and Gear Set Data}

Key to much of the work so far are the constants associated with the motor and gear set, $K_{t}$, $K_{v}$, $R$, and $L$.
Here we are using a \href{https://www.pololu.com/product/3237}{Pololu  4.4:1 metal gear motor}.  

Pololu gives the following parameters for the 4.4:1 gear motor: \\
weight = 95g \\
gear ratio = 4.4:1 \\
No-load speed @ 12V = 1700 rpm (178 rad/sec)\\
No-load current @ 12V = 0.2 A \\
Stall current @ 12V = 2.1 A \\
Stall torque @ 12V = 11 oz in (0.07768 Nm)\\
Encoder frequency = 211.2 counts/rev of gearbox shaft\\

A number of the motor constants can be calculated from the published Pololu parameters.  However, it
should  be noted that, for inexpensive motors, the actual motor parameters may vary from the 
published data.  In any event, the motor constants will be calculated here and then later compared
with measured data.

$K_{f}$ can be calculated directly from the stall current, gear ratio, and torque: $K_{f}$ = 0.07768 Nm /  2.1 A = 
0.0370 Nm/A.  $K_{v}$ can be set equal to $K_{f}$, or 0.0370 Vs.

The motor winding resistance can be determined from the rated voltage and the stall current, as no back-EMF is occurring at stall
conditions.  Thus, $R$ = 12 V / 2.1 A = 5.7 ohms.

\section{Pendulum Constants}
A multitude of other values were calculated in MATLAB.  \\

\begin{tabular}{l l}
$m$ & 0.517327 kg \\
$l$ & 0.319038 m \\
$I_{c}$ & 0.046508 kg m\textsuperscript{2} \\
$I_{f}$ & 0.000164 kg m\textsuperscript{2} \\
$g$ & 9.81 m s\textsuperscript{-2} \\
\end{tabular}

\section{Measuring Motor Constants}
\label{appendix:measure}
Measurements were made to determine a number of motor constants, including $r$, $l$, and $K_{v}$.  

$r$ was measured using an EXTEC LCR meter, on the $R_{DC}$ setting, as 5.82 $\Omega$. $l$ was 
measured with the same instrument as 5.994 mH at 1kHz.  This gives a motor electrical time constant $l/r$ of 0.001 sec.  This is the time taken by the current in the motor to go from rest to 63\% of the final steady-state current.

$K_{v}$ was measured by driving a motors with a constant voltage and
varying loads while measuring $V$, $i$, and $\omega$.  

The motor was driven with a 12 V power supply.  The current was measured by the power supply.  Measuring current in this manner can have larger uncertainties, but comparing with measurements from a $\mu$Current DVM adapter indicated that the power supply current measurement was reasonable.  

$\omega$ was measured using the motor's encoder and an Arduino.  The encoder measured the shaft speed, not the gear-set speed.  However, a conversion coefficient of 211.2 counts/revolution was used to convert the encoder pulse rate to gear set rotation speed.

The following table shows the results for three different loads.  The first load was just rotor friction.  The second load added the Pololu hub adapter.  The third load included a plastic wheel attached to a propeller to increase the drag.
The resulting measured values are as follows: \\

\begin{tabular}{|c|c|c|c|c|c|}
\hline
Case & $v$ & $i$ & speed & $\omega$ & $\omega$ \\
      & (V) &  (A) & (counts/sec) & (RPM) & (sec\textsuperscript{-1}) \\
\hline
1    & 11.95 & 0.0675 & 5,942.2   & 1,688.1   & 176.74 \\
2    & 11.95 & 0.075   & 5,923.58 & 1,682.83 & 176.19 \\ 
3    & 11.95 & 0.153   & 5,574.88 & 1583.77  & 165.82 \\
\hline
\end{tabular}

Calculating $K_{v}$ can be approached two ways.  The first is to solve \eqref{motor} using the measured
value of $R$.  The resulting values of $K_{v}$, one for each case, are:

\begin{tabular}{|c|c|}
\hline
Case & $K_{v}$  \\
         & (V sec) \\
\hline
1    & 0.0654  \\
2    & 0.0653  \\
3    & 0.0667  \\
\hline
\end{tabular}

A second approach is to use two cases in \eqref{motor} and solve simultaneously for $R$ and $K_{v}$.
Cases 1 and 3 were chosen because of the largest difference in $i$, attempting to ensure that the two
cases are independent.  This results in a values of $r$ = 8.24 $\Omega$ and $K_{v}$ = 0.0645 V sec.

The value of $K_{v}$ is fairly consistent with the values determined in the first approach, but the value
of $r$ appears to be high.  This may be caused by the limited change in $i$ in the data.  Use of a larger
load torque might result in a larger value of $i$ and a better estimate of $r$.  However, for the purposes
of this work the following values will be used:

\begin{tabular}{|c|c|c|}
\hline
r                   & $K_{v}$  & $K_{t}$ \\
($\Omega$)   & (V sec)   & (N m A) \\
\hline
5.82    & 0.0667  & 0.0667  \\
\hline
\end{tabular}

\section{Measuring Motor Friction Constants}
\label{appendix:friction}
Friction in the motor was evaluated by measuring the supply current as a function of motor speed.
The friction force is related to the motor current as $F = K_{t} i$.  The measurement was performed
by using a power supply with a variable current limit.  For various currents the speed of the motor
was measured by monitoring the motor encoder output with an Arduino.  The current was measured
both at the power supply as well as with a $\mu$Current DVM adapter.

The following data was collected:

\begin{tabular}{|c|c|c|c|c|c|}
Supply Voltage & Supply Current & $\mu$Current & Speed & Speed & Speed\\
(V) & (A) & (A) & (pulse/sec) & (rpm) & radians/sec\\
\hline
10.90 & 0.068 & 0.0676 & 5417 & 1538.9 & 161.16\\
10.04 & 0.063 & 0.0627 & 5001 & 1420.7 & 148.78\\
9.09 & 0.058 & 0.0596 & 4520 & 1284.1 & 134.47\\
7.93 & 0.056 & 0.0562 & 3937 & 1118.5 & 117.13\\
6.99 & 0.055 & 0.0550 & 3465 & 984.4 & 103.08\\
6.00 & 0.051 & 0.0521 & 2953 & 838.9 & 87.85\\
5.00 & 0.047 & 0.0500 & 2437 & 692.3 & 72.50\\
4.04 & 0.046 & 0.0483 & 1960 & 556.8 & 58.31\\
3.57 & 0.046 & 0.0486 & 1701 & 483.2 & 50.60\\
3.02 & 0.047 & 0.0481 & 1421 & 403.7 & 42.27\\
2.52 & 0.045 & 0.0459 & 1169 & 332.1 & 34.78\\
2.02 & 0.042 & 0.0437 & 910 & 258.5 & 27.07\\
1.51 & 0.039 & 0.0409 & 662 & 188.1 & 19.69\\
1.02 & 0.034 & 0.0366 & 414 & 117.6 & 12.32\\
0.47 & 0.031 & 0.0328 & 148 & 42.0 & 4.40\\
\end{tabular}

The encoder speed, in pulses/sec, was converted to RPM using the encoder frequency of 211.2
counts/revolution.

The Excel regression function was used to fit the $\mu$Current current measurement as a function
of the speed in radians/sec.  The regression intercept represents the fixed Coulomb friction and the
slope represents the viscous friction.  The regression results were 2.47E-3 N m and 1.20E-5 N m/(radian/sec),
after converting from current using $K_{t}$.  The coulomb friction represents approximately 3\% of the 
motor stall torque.  At the motor's no-load speed the viscous friction would double the total friction to 
approximately 6\% of the motor stall torque.  The viscous friction coefficient is significantly larger than
the value of 9.06E-7 N m/(radian/sec) measured in Reference \cite{twoWheeled}.  This may be due to
the gearbox associated with the motor used in the current work.  In any event, the friction will be included
in the system modeling.

\section{Arduino Code for Measuring RPM}

The following is an Arduino sketch used to monitor the speed of a dc motor.  The sketch is designed
to work with either an Arduino Uno or an Arduino Mega. The motor wiring described in the comments
referrs to the wiring of the Pololu 25D 4.4:1 metal gear motor.  The output is in position change 
per second, where the motor has 211.2 counts/rev of gearbox shaft. \\

\lstinputlisting{../arduino/rpm/rpm.ino}

\section{Reaction Wheel Design Options}

The initial reaction wheel design was modeled after XXXX, with modifications to allow the reaction wheel
to mate properly with a Pololu motor hub.  The reaction wheel is shown in Figure \ref{reactionWheel}.
The reaction wheel body is aluminum an outer diameter of 90 mm, a width of 18 mm, and an annular thickness of 7 mm. 
Fusion 360 reports the mass of the reaction wheel to be 0.09391 kg (assuming a density of 2.7 g/cc).
The moment of inertia around the centerline is 1.562E-4 kg/m2.

An alternate, simpler design (although less elegant) is shown in Figure \ref{simpleReactionWheel}.
Fashioned from carbon steel with a density of  7.85 g/cc, the diameter of the wheel is 90 mm and the
thickness is 3.175 mm (1/8").  The reaction wheel mass is 0.175 kg and the moment of inertia 
around the centerline is 1.605E04 kg/m2.  The simpler design with only a small change in the moment
of inertia permits an easier fabrication at a cost of a doubling of the reaction wheel mass.

 
    \captionof{figure}{Aluminum Reaction Wheel}  
    \label{reactionWheel}

 
    \captionof{figure}{Simplified Carbon Steel Reaction Wheel}  
    \label{simpleReactionWheel}

\end{appendices}

\end{document}

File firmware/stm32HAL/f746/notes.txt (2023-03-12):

Notes on the Project Design

- An STM32 Project
The original Arduino code worked, but it was a bit of a dog's breakfast.
Moving away from the Arduino ".ino" format allows for what I believe to be a 
cleaner source structure.

- Using the STM32 HAL library
After writing a few low level libraries, I wanted to try taking 
advantage of a "canned" library for the peripherals.  Many think that this incurs
a lot of overhead.  Time will tell if it will be a significant impediment.  Note that
I did use the LL routines for the USART, as the HAL library didn't provide enough
flexibility to implement the terminal process that I wanted.

- Using STM32CubeIDE-generated code
The configurator built into the STM32CubeIDE makes it very easy to experiment with
different hardware configurations.  The auto-generated code then makes the base
configuration simple.  I've kept my code, to the extent possible, separate from
the auto-generated code.  The auto-generated code is in the "Core" folder, libraries
are in the "Libs" folder, and the application code is in the "Project" folder.

- This is a C++ project
Most embedded software seems to be written in C, and I would have used C if I could.
However, to avoid straying too far from the original Arduino software I needed to 
use the MPU6050 library from https://github.com/jrowberg/i2cdevlib
The STM32 and STM32HAL versions of the i2cdevlib MPU6050 are not complete, missing
some of the Digital Motion Processor (dmp) routines.  As an alternative I used
the Arduino C++ routines modified as necessary to call the HAL I2C library.  As
C routines can't call C++ classes, the code ended up being written in C++.

- But, but, isn't the main routine (generated by the IDE) written in C?
Yes.  The main routine calls a procedure, app_entry(), which is the entry point
into the C++ code.  app_entry() is defined in appEntry.hpp to have an extern "C"
interface, allowing this C++ routine to be called from main.c.  It's a cludge, but
it works.

- Why not just convert main.c to main.cpp and avoid app_entry()?
Every time the hardware configurator regenerates code to match an modified
hardware configuration, it generates main.c, not main.cpp.  This would leave any
user modifications to the main.cpp file stranded.  Having main() call app_entry()
isn't the cleanest code, but it's better than using multiple Arduino .ino files.

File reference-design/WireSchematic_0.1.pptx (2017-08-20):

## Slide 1

Encoder Interrupt (A) - R

Encoder A – Yellow wire from encoder
Encoder B – Green wire from encoder

IMU Interrupt

Motor PMW - R

Motor PMW - L

Encoder (B) - R

Encoder Interrupt (A) – Left

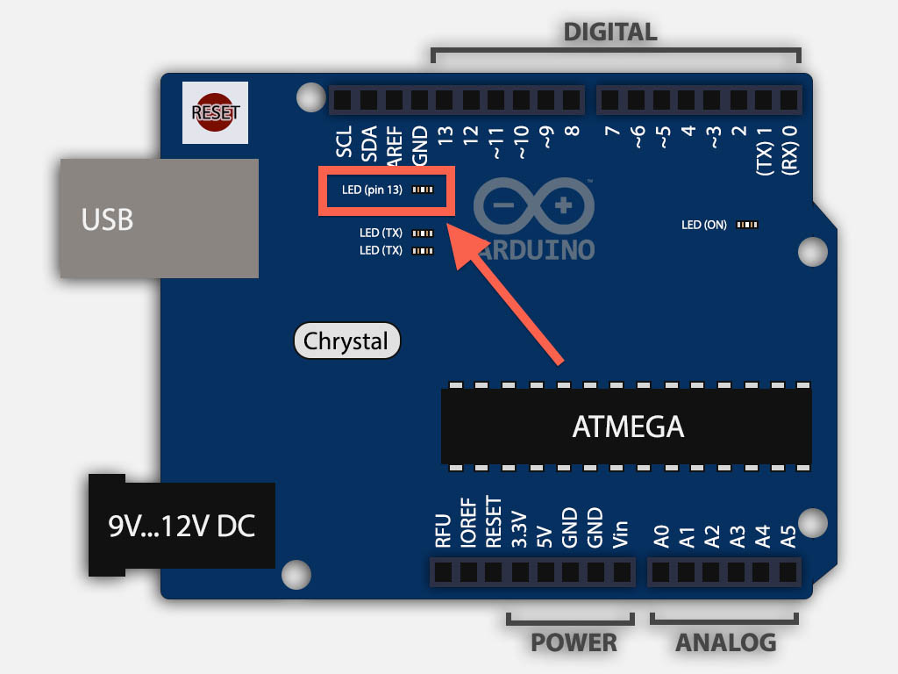
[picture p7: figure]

In4

In3

In2

In1

MOTOR 1 - Left

Serial

MOTOR 2 - Right

Power Supply +

Power Supply -

IMU - SCL

IMU

Current - R

IMU - SDA

Current - L

Encoder (B) - L

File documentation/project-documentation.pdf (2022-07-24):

# Oh, What a Bot!

### HackRVA.org

1

## Contents

List of Symbols | 3
1 Introduction | 5
2 Pendulum Dynamics | 8
3 Motor and Flywheel Dynamics | 10
4 Motor Control | 11
5 Modeling in the Frequency Domain | 13
6 State Space Model | 20
7 Implementation Details | 22
Appendices | 24
A Motor and Gear Set Data | 24
B Pendulum Constants | 26
C Measuring Motor Constants | 27
D Arduino Code for Measuring RPM | 31
E Reaction Wheel Design Options | 34

2

## List of Symbols

The following list describes several symbols that will be used later within the body of the document

Physics constants

g | Gravitational constant (m s⁻²)

Transfer Functions

C(s) | control function
M(s) | motor transfer function
P(s) | pendulum transfer function
R(s) | rotor transfer function
T(s) | open loop transfer function

Other symbols

ηg | gear efficiency
ηm | motor efficiency
ω | motor rotation speed (rad s⁻¹)
ϕ | flywheel angle (rad)
θ | pendulum angle (rad)
A | coulomb friction coefficient (N m)
B | rotational friction coefficient(N m rad⁻¹ s)
F | environmental forces on the pendulum
i | motor current (A)
Ic | moment of inertia of the pendulum (kg m²
)
If | moment of inertia of the reaction wheel (kg m²
)
| 3

Kω | rotor velocity feedback gain
Kt | motor torque constant (N m A⁻¹)
Kv | motor voltage constant (V rad⁻¹ s)
L | armature inductance (H)
l | distance from the pivot point to the center of pendulum mass (m)
m | total mass of inverted pendulum (kg)
r | armature resistance (Ω)
T | total motor torque (N m)

Tfriction torque lost to motor and gear friction (N m)

Tshaf t | torque available to the flywheel (N m)
u | controller output
v | voltage supplied to the motor (V)
x | net torque applied to the pendulum (N m)

4

## 1 Introduction

This article describes the development of a control system model for an reaction wheel pendulum, shown in Figure 1. A reaction wheel pendulum is a variation of a simple pendulum, balanced upright, with rotating wheels at the top in place of the pendulum bob. Each wheel is driven by a separate motor. The pendulum is inherently unstable in the upright position -gravity will pull the pendulum over if it is not perfectly balanced. Thus, a control system is needed to accelerate the reaction wheels, applying torques as needed to the pendulum so as to keep it upright. The reaction wheels are mounted at right angles to each other, providing the ability to correct the alignment of the pendulum in any direction.
The pendulum physical structure includes a rod, an accelerometer, and two flywheels. Each flywheel is comprised of a motor mount, a DC brushed motor, and a reaction wheel. The flywheel assemblies are mounted at the
top of the rod at right angles to each other and the rod. The DC motors are
wired to a motor controller and an Arduino. The Arduino is also wired to
the accelerometer, which is located at the top of the rod. | needs
| a fig-
| ure
| num-
| ber

The basics of the pendulum control system is outlined in Figure ??. The system can be controlled by adjusting the voltage. An additional input F is included to describe random environmental forces that may affect the pendulum. The random forces may result in the desired angle of the pendulum not being achieved. More accurate control will result from feeding the resulting pendulum angle back into the control system so that the input voltage is continuously adjusted until the desired pendulum angle is achieved. This is shown in Figure 2.
In this case, however, the goal is for the pendulum to remain vertical with as little wobble as possible. The real control comes into play when correcting for the stray forces on the system. Hence, the control system can be reformulated as shown in Figure 3, commonly known as a Regulator Problem. This structure emphasizes the environmental forces as the primary input into the
system and that the feedback is primarily intended to compensate for those
forces. | Figure
| 3 is
| miss-
| ing a
| feed-
| back
| arrow
5

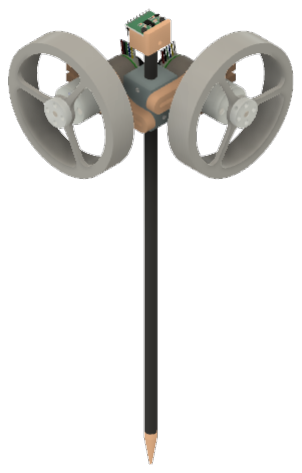
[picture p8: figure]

Figure 1: Sketch of the Pendulum

6

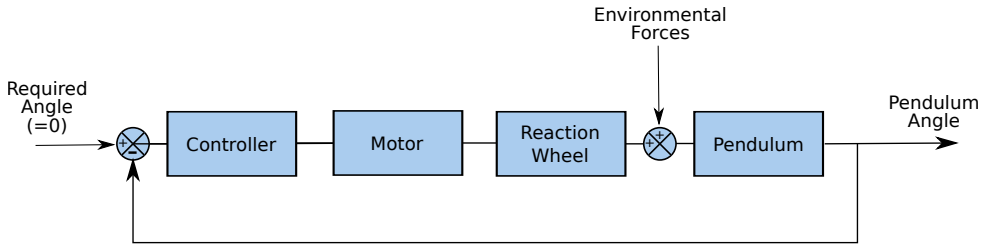
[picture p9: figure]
Pendulum Angle; Reaction Wheel; Required Angle (=0); Environmental Forces; Controller; Motor; Pendulum ⁺

Figure 2: Simplified Pendulum Model

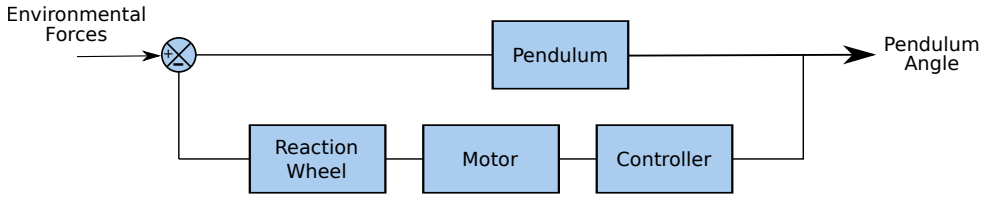
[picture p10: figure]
Environmental; Forces; Pendulum; Angle; Reaction; Wheel; Motor; Controller; Pendulum -

Figure 3: Regulator Model

7

## 2 Pendulum Dynamics

More detail can be added to the regulator control system description by building a mathematical model of the the pendulum. Figure 4 shows a simplified sketch of the inverted pendulum. Reference [2] contains a summary of the model dynamics for the balancing pencil. The model dynamics can be summarized as
mglsin θ + F − Ic
¨θ = Ifϕ¨ | (1)

Other references may have alternate formulations using different definitions for θ and ϕ.

1

After linearizing the equation by noting that sin θ ≈ θ for small angles, the transfer function for the pendulum is then

m g lθ + F − Ic

¨θ = Ifϕ¨ | (2)

The reaction wheel can be continuously revolving, making the reaction wheel
angle ϕ less useful as a control parameter. In its place we will use ω = ϕ˙ | .

m g lθ + F − Ic

¨θ = Ifω˙ | (3)

For ease of use in later analysis, it is beneficial to split (3) into two parts:

m g lθ + x(t) = Ic

¨θ | (4)
x(t) = F − Ifω˙ | (5)

where x(t) is the net torque applied to the pendulum. The sign convention is important; a positive torque x(t) will accelerate the pendulum in the direction of the positive pendulum angle. However, the sign convention in (5) indicates that a positive acceleration of the rotor will result in a negative acceleration of the pendulum.
Note that if the pendulum is not vertical (i.e. θ = 0) gravity will begin to pull the pendulum over. Correcting this requires accelerating the flywheel

1Reference [1] has a slightly different formulation for the model dynamics; the sign of the gravitational term is positive rather than negative. This difference is caused by Reference [1] defining the angle from the downward, resting position while Reference [2] defines the angle from the vertical. The cosines of angles differing by π have opposite signs.

8

to apply torque to the pendulum. A flywheel turning at a constant velocity applies no torque to the pendulum and will not alter the movement of the pendulum.


Figure 4: Simplified Pendulum Model

9

## 3 Motor and Flywheel Dynamics

Reference [2] models the motor as

If ϕ η ¨ m ηg = Kt i | (6)

This formulation appears to have problems, as a reduction in the motor and gear efficiencies results in a greater flywheel acceleration for a given motor current. Similarly, a gear ratio above unity would decrease the flywheel acceleration for a specified motor current/torque, which is non-physical. The equation can be altered to correct these issues, resulting in the following:
If ϕ¨ = ηm ηgKt i | (7)

However, this format may not be the easiest to implement, as the motor and gear efficiencies are not known. Reference [1] takes a different approach,²

If ϕ¨ = Tshaf t | (8)

Where the earlier format dealt with motor/gear efficiencies using ηm and ηg, Reference [1] develops a correlation of friction in terms of torque required to maintain a given ϕ˙
. Here the torque will be reformulated as
Tshaf t = T − Tfriction | (9)
Tfriction = A sgn(ϕ˙ − ˙θ) + B(ϕ˙ − ˙θ) | (10)
T = Kt i | (11)
Note the use of (ϕ˙ − ˙θ). Friction is dependent on the relative motion of the motor armature and the motor frame. If the pendulum angular velocity ϕ˙
| is
equal to the reaction wheel angular velocity ˙θ there will be no relative motion between the motor armature and frame; no friction will occur.
Combining equations,
If ϕ¨ = Kt i − A sgn(ϕ˙ − ˙θ) − B(ϕ˙ − ˙θ) | (12)

Again, using the notation ω = ϕ˙
,
If ω˙ = Kt i − A sgn(ω − ˙θ) − B(ω − ˙θ) | (13)
As will be seen, this equation is easier to implement because Kt | , A, and B
can be measured experimentally (see Appendix C).

2Note that there is no term in (8) that represents torque associated with external work done by the shaft. Hence this formulation is limited to flywheels that are reasonably aerodynamic (e.g. not something that acts as a propeller).

10

## 4 Motor Control

The previous chapter determined the relationship between the motor current and the acceleration of the flywheel. However, the motor will be not be controlled via motor current. Instead, a motor controller will be used to control the motor by adjusting the motor voltage via a PWM signal. The equivalent, average voltage will then regulate the motor. Following Reference [1], but recognizing the motor is at the end of a pendulum, the relationship between motor current and voltage is

L

di
dt + r i = v − Kv (ω − ˙θ) | (14)

Normally the inductance of the motor is much lower than the resistance, such that L/r ∼ 0.001 sec. In such cases it is acceptable to ignore the time dependence of the current and write

r i = v − Kv (ω − ˙θ) | (15)

Solving for i:

i =

v
r

−

Kv (ω − ˙θ)

r

(16)

Combining with (13)

If ω˙ = Kt

v
r

−

Kv (ω − ˙θ)

r

!
− A sgn(ω − ˙θ) − B(ω − ˙θ) (17)

Rearranging,

If ω˙ +

B +

KtKv
r

(ω − ˙θ) + A sgn(ω − ˙θ) = Kt
r
v | (18)

Not all of the voltage results in acceleration of the reaction wheel. As the reaction wheel velocity increases, an increasing amount of the voltage (and the resulting torque) is consumed by friction and the back EMF.

The voltage used to drive the motor is determined by the controller. Here the voltage will be set to the output of the controller

v = u | (19)

11

Substituting into (18)

If ω˙ +

B +

KvKt
r

(ω − ˙θ) + A sgn(ω − ˙θ) = Kt
r
u | (20)

The simple substitution of u for v does not seem to have much purpose at this point in the analysis, but will be useful when complex controllers are evaluated.

It is useful to assume that the control function can adjust the demand voltage by adding or subtracting a constant, depending on the current spin direction of the reaction wheel. This means that −A sgn(ϕ˙) is folded into u for the purposes of this analysis. Our motor control equation is then

If ω˙ +

B +

KvKv
r

(ω − ˙θ) =
Kt
r
u | (21)

12

## 5 Modeling in the Frequency Domain

The primary objectives of a control system for the pendulum should be to stabilize the upright position of the pendulum and recovering from external forces on the pendulum. In addition, the control system should be designed to deal with a number of physical limitations of the physical components of the pendulum. Specifically,

- the motor voltage is limited to maximum value,
- the rotor velocity has a practical upper limit.

The stability of the system shown in Figure 3 can be evaluated by examining the open loop transfer function

T(s) = P(s)C(s)M(s)R(s) | (22)

The control system in terms of these transfer functions is shown in Figure 5.

The controller, at this point in the analysis, is assumed to be a pass-through, or
u = θ | (23)

Hence, the controller transfer function is

C(s) = u(s)
θ(s)
= 1 | (24)

The pendulum transfer function can be derived from (4)

m g lθ(s) + x(s) = Icθ(s)s

2
(25)

Ignoring the environmental forces, the pendulum transfer function is

P(s) = θ(s)
x(s)

=

1
Ics
2 − mgl | (26)

The rotor transfer function can be derived from (5) by noting that the torque generated by the flywheel is

x(s) = F(s) − Ifω(s)s | (27)

13

R(s) = x(s)
ω(s)
= −If s | (28)

Note that the transfer function for the rotor in (28) is negative. Combined with the summing junction shown in Figure 5, this produces a negative feedback control system.

The motor transfer function must be derived from (21). However, in (21) ω is a function of both θ and u, preventing the determination of a single-input, single-output transfer function. One solution is to make the approximation ω ≈ (ω − ˙θ). The reaction wheel may rotate at hundreds of RPM, while the pendulum is expected to deviate from vertical for only brief periods. With this approximation the motor transfer function can be derived from (21) as

If ω(s)s +

B +

KvKt
r

ω(s) =
Kt
r
u(s) | (29)

M(s) = ω(s)
u(s)

=

Kt
r
If s + ( KvKt
r + B)

(30)

Using (24), (26), (28), and (30) results in

T(s) =

−(

1
Ic

)( Kt
r

)s
(s

2 −

mgl
Ic

)(s + ( KvKt
rIf

+

B
If

))

(31)

Substituting in values from the appendixes, the transfer function for the pendulum is
T(s) = | −0.1731s
s

3 + 3.113s

2 − 34.8s − 108.3

(32)

The numerator of the transfer function is the characteristic equation that, when factored, is (s − 5.899)(s + 5.899)(s + 3.113).
Using the root locus technique and the open loop transfer function, Figure 6 shows the behavior of the closed loop poles as a function of feedback gain. Note that one pole is always in the right half of the plane, indicating that the system is unstable regardless of the magnitude of the gain.

The system might be stabilized by using both proportional and derivative, or PD, feedback. The control function would be:

u = θ + p

˙θ | (33)

14

thus
C(s) = 1 + ps | (34)

Rearranging,

C(s) = p

s +

1
p
(35)

indicating a zero at 1/p and a gain of p. The results are sensitive to the placement of the zero. Placing the zero to the right of the pole at -5.8993 eliminates any oscillation but does not remediate the pole in the right half of the plane. Placing the zero to the left of the pole at -5.8993 results in a much faster response but can result in oscillations (Figure 7). Again, the pole in the right half of the plane is not remediated.

One additional possibility for resolving the issue of the zero at the origin would be to implement a PID controller.

u(t) = θ(t) + q

Z
θ dt + p

˙θ

then
C(s) = 1 + q
s
+ ps | (36)

Rearranging,

C(s) = p

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
(37)

This controller would have two zeros that can be placed as required and a pole that would cancel the zero at the origin. If the zeros are placed to the left of the pole at -4.7303, then the system may stabilize. However, in the
real world the original zero may not be exactly at the origin and the poles
in the left side of the axis may not be exactly where they are expected (due
to nonlinearities, etc.) leading to a less-than robust control system. | verify
| this
Finally, it is possible to include feedback from the other monitored and controlled variable, the rotor velocity. Unfortunately, to continue to evaluate
the system using a root locus analysis, the feedback from the rotor velocity cannot be included directly in C(s), as it would introduce a second input into the transfer function. Instead, the definition of the motor voltage v is modified to include the effect of the rotor velocity feedback
v = u + Kωω | (38)

15 where u continues to represent the output of a PID controller using θ as an input and Kωω is an additional feedback from the rotor velocity. This results in (21) transforming into

If ω˙ +

B +

K²
v
r

ω + A sgn(ω) =
Kv
r
(u + Kωω) | (39)

The motor transfer function is then

If ω(s)s +

B +

K²
v
r

ω(s) =
Kv
r
(u(s) + Kωω(s)) | (40)

Rearranging terms,

M(s) = ω(s)
u(s)

=

Kv
If r

s + ( 1
If

)( K²
v

r −

KvKω
r + B)

(41)

Using (35), (26), (28), and (41), the open loop transfer function is now

T(s) =

−(

Kp
Icr

)(s +

1
p

)s

s

3 + ( Br−KKω+K²
If r

)s

2 − (

mgl
Ic

)s − (

Br−KKω+K²
If r | −

mgl
Ic

)

(42)

Figure 8 shows the root locus with p = 1/4.5 and Kω = 0.075. With a controller gain³ of 370 the controlling close loop poles are at -11.3, -1.33,

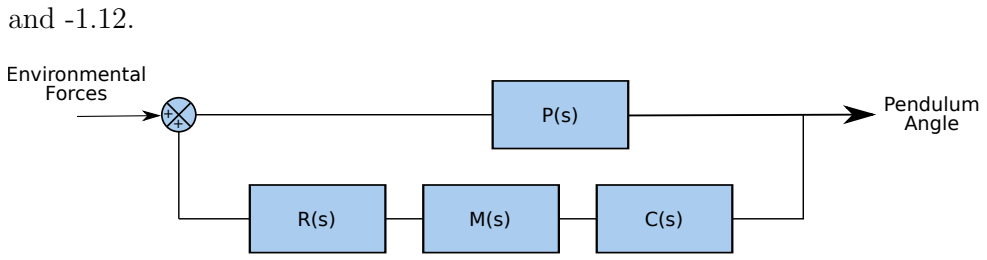
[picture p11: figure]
and -1.12.; Environmental; Forces; Pendulum; Angle

Figure 5: Control System Modeled as Transfer Functions

3The gain given here is in addition to the system gain modeled in (42).

16

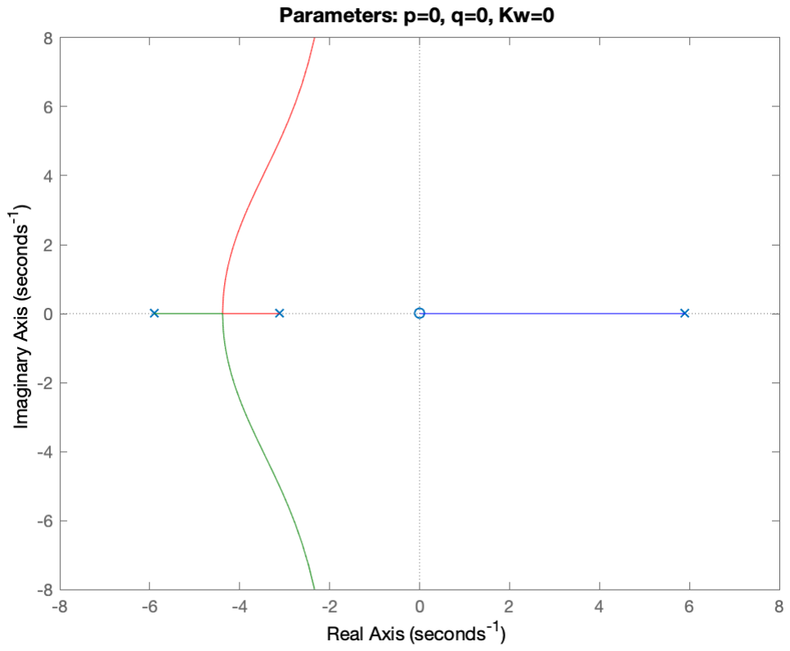
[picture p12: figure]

Figure 6: Root Locus Plot With Proportional Feedback

17

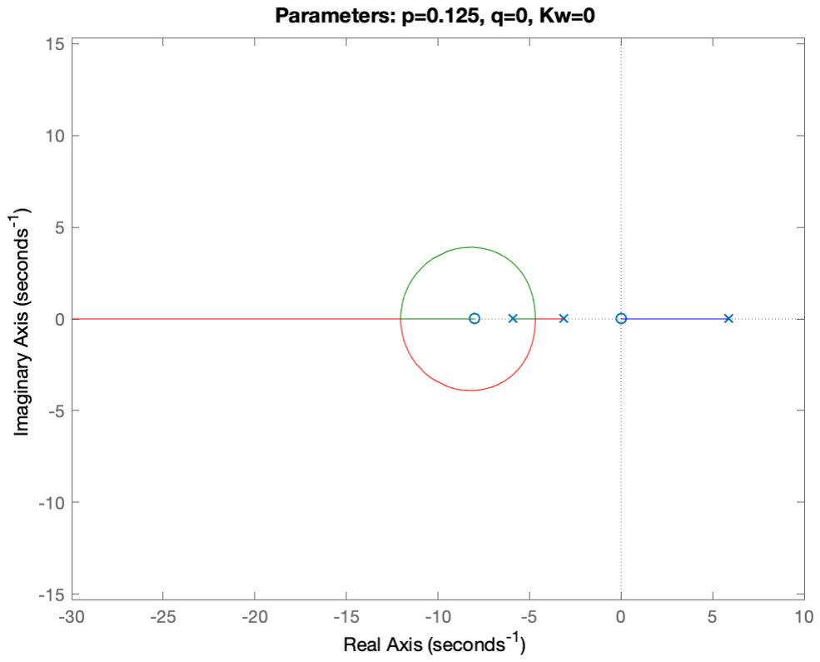
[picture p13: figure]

Figure 7: Root Locus Plot With PD Feedback

18

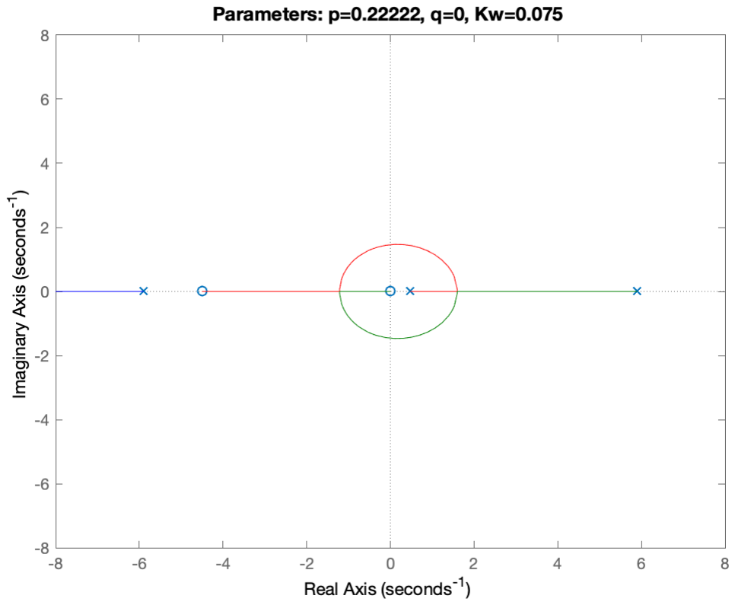
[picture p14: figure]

Figure 8: Root Locus Plot With PD and Rotor Velocity Feedback

19

## 6 State Space Model

A State Space model can be constructed from equations (18) and (3). The state space variables are ω, θ, and ˙θ. The state space model is then

x˙m = Amx + Bmv | (43)

where xm = (ω, θ, ˙θ)
T and

Am =

−

B
If

−

KvKt
If r

0

B
If

+

KvKt
If r
0 | 0 | 1

B
Ic

+

KvKt
Icr
| mgl Ic
−

B
Ic
| | −

KvKt
Icr
- (44)

Bm =

Kt
If r
0
−

Kt
Icr
- (45)

However, measured sensor data from motor encoder signals are proportional to the relative velocity of the reaction wheel, ωr = ω − ˙θ. Changing the state space variables to x = (ωr, θ, ˙θ)
T
is performed using a transformation matrix x = P xm where

P =

1 0 −1
0 1 | 0
0 0 | 1
- (46)

From Reference [6] the new state space model is then

x˙ = Ax + Bv | (47)
y = Cx + Dv | (48)
where x = (ωr, θ, ˙θ)
T
, y = (ωr, θ)

T

A = P AmP

−1
(49)
B = P Bm | (50)

resulting in

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
KvKt
If r −

KvKt
Icr −

mgl
Ic

0
0 | 0 | 1

B
Ic

+

KvKt
Icr
| mgl Ic | 0

- (51)

20

B =

Kt
If r +

Kt
Icr
0
−

Kt
Icr
- (52)

C =

1 0 0

0 1 0
(53)

D =

0
0
(54)

21
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

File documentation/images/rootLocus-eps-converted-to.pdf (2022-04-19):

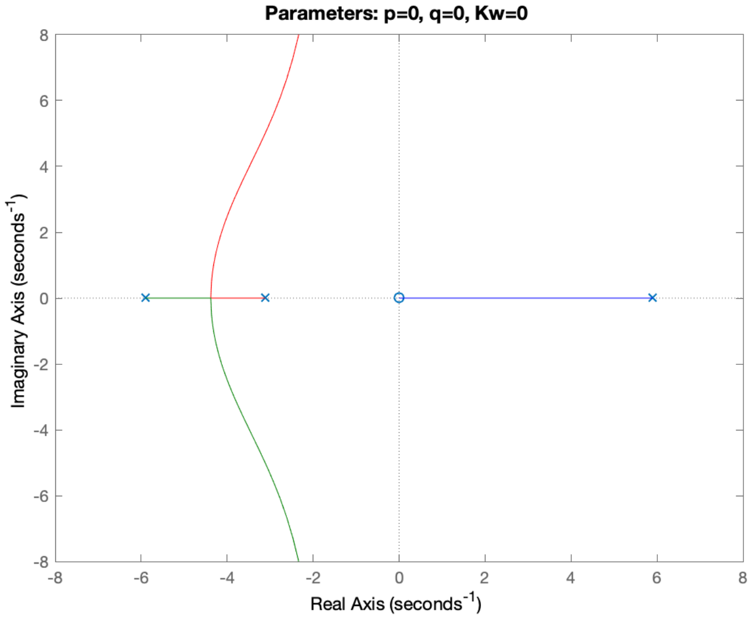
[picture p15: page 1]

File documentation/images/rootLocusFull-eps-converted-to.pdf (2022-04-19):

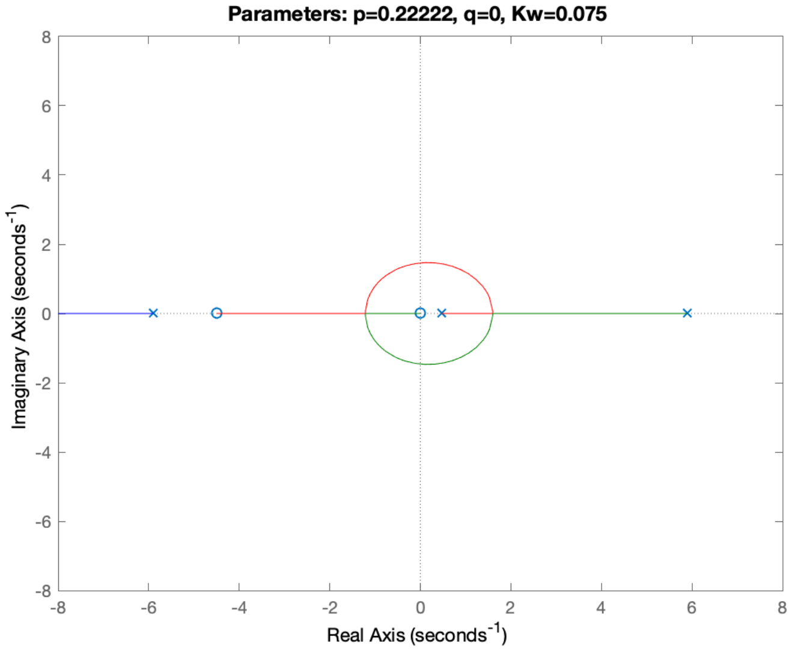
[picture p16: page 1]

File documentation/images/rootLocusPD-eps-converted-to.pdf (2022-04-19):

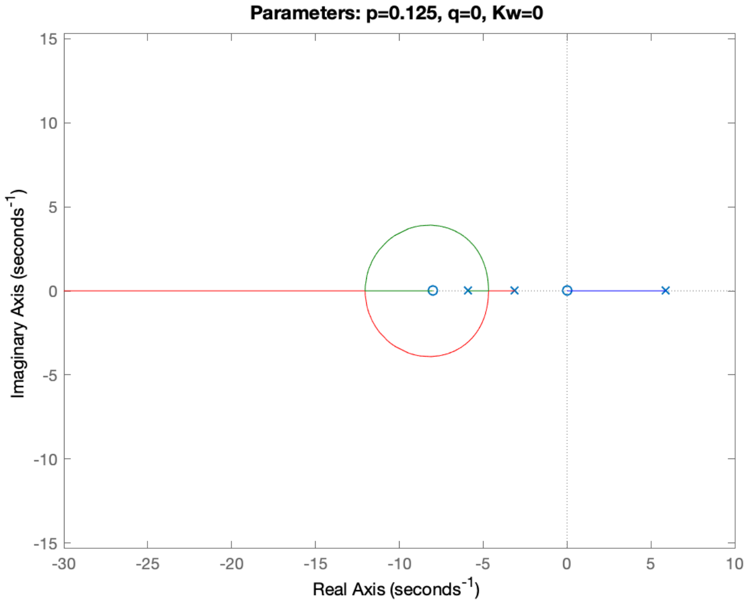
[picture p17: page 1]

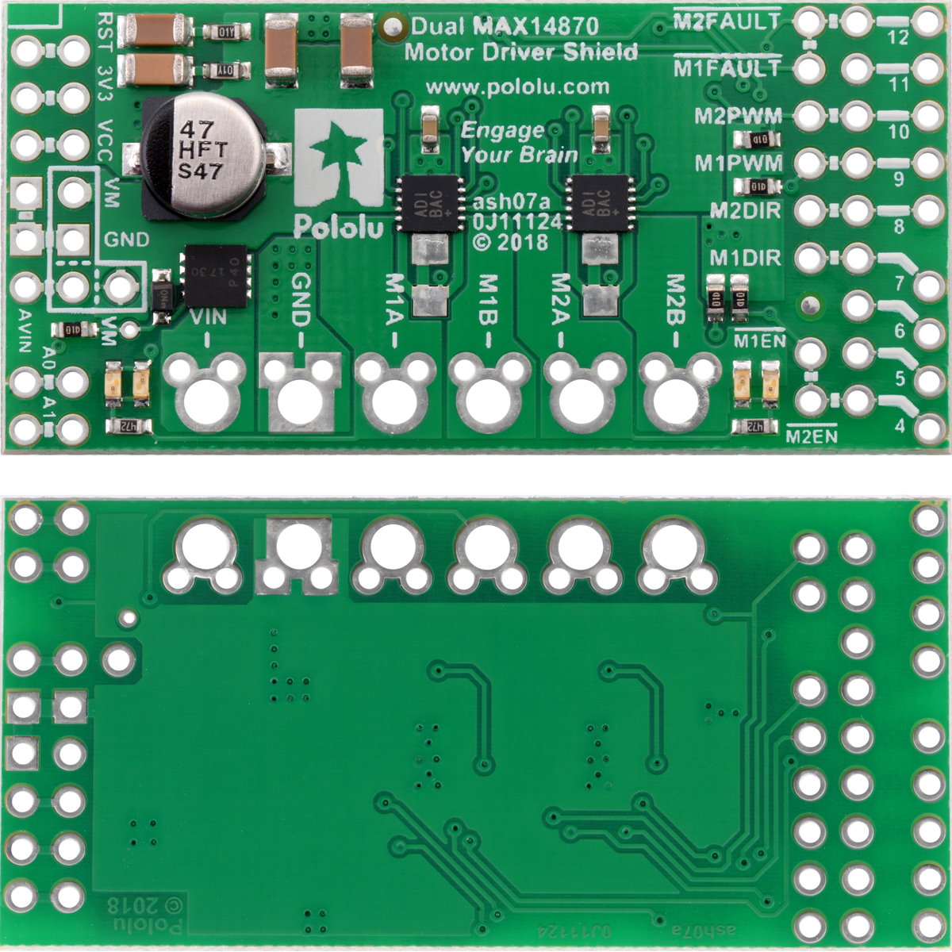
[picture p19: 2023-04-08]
references/MAX14870_motor_driver/0J8597.1200.jpg

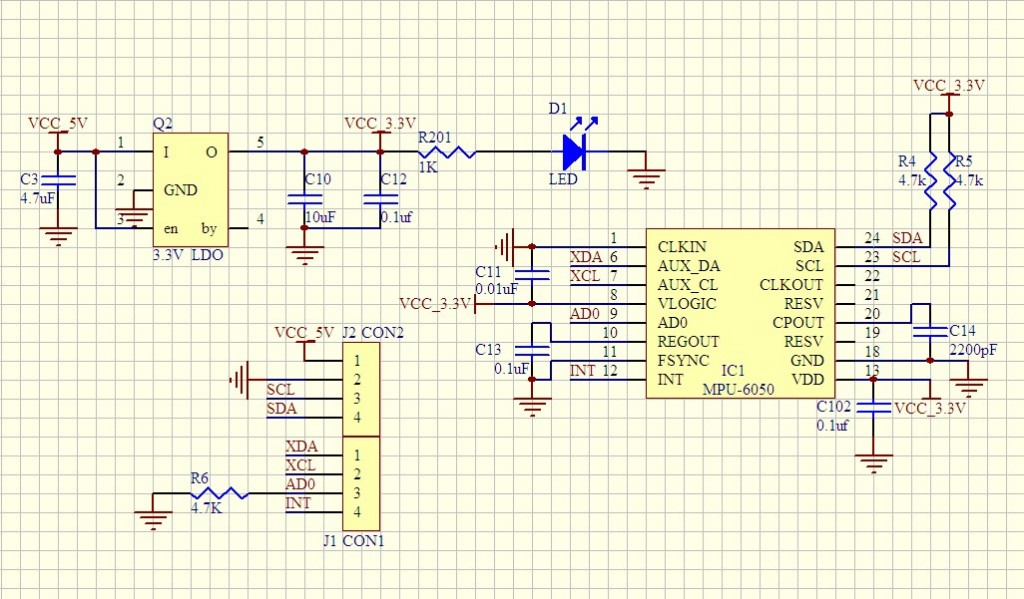
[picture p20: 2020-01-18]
references/IMU/MPU6050-V1-SCH-1024x599.jpg

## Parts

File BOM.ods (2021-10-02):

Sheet: Sheet1
 | COTS Components
P/N | Desc | Supplier | Supplier P/N | Count | Unit Cost | Unit | Extended Cost | Mass - g (each) | Mass (total) | Note
1 | Gyro, GY-521 | amazon |  | 1 |  | ea
2 | clamp screw 2.5x0.44, 16mm | McMaster Carr | 91292A018 | 2 | 3.22 | 50 cnt | 3.22 | 0.735 | 1.47
3 | clamp lock nut, M2.5 | McMaster Carr | 93625A102 | 2 | 10.25 | 100 cnt | 10.25 | 0.34 | 0.68
4 | motor mount screw m2.5x0.45, 12mm | McMaster Carr | 91292A016 | 4 | 5.15 | 100 cnt | 5.15 | 0.59 | 1.18
5 | shaft (1 ft) | McMaster Carr | 7237K33 | 1 | 2.11 | ea | 2.11 | 7.99 | 15.97
6 | set screw, M4x0.7, 4mm | McMaster Carr | 92015A110 | 3 | 9.70 | 100 cnt | 9.70 | 0.22 | 0.44
7 | gyro screws, m2x0.4, 6mm | McMaster Carr | 91292A831 | 2 | 6.38 | 100 cnt | 6.38 | 0.22 | 0.44
8 | Motor Clip | Note 1 | --- | 2 | --- | ea | --- | 5.00 | 10.00
9 | reaction wheel | Note 1 | --- | 2 | --- | ea | ---
10 | shaft point | Note 1 | --- | 1 | --- | ea | ---
11 | gyro mount | Note 1 | --- | 1 | --- | ea | ---
12 | Motor Mount | Note 1 | --- | 1 | --- | ea | ---
13 | DC motor | Pololu | 3237 | 2 | 34.95 | ea | 69.90 | 96.35 | 192.70
14 | hub assembly (2 pack) | Pololu | 1081 | 1 | 6.95 | ea | 6.95 |  |  | could be p/n 1997 (metric)
15 | Motor Driver | Pololu | 2507 | 1 | 49.95 | ea | 49.95 |  | ---
16 | Arduino | spare parts | --- | 1 | --- | ea | --- |  | ---
17 | Cabling | spare parts | --- | 1 | --- | ea | ---
18 | Power Supply | spare parts | --- | 1 | --- | ea | --- |  | ---
 |  |  |  |  |  |  | 163.61 |  | 222.88
Note 1: | These parts are to be fabricated.
 | Raw Materials
P/N | Desc | Supplier | Supplier P/N | Count | Unit Cost |  | Extended Cost | Notes
1 | ABS Sheet, 1/4"x12"x12" | McMaster Carr | 8586K171 | 1 | 15.14 |  | 15.14 | Used for motor clamps
2 | HDPE Bar,1"x3/4"x 1 ft | McMaster Carr | 8671K15 | 1 | 2.49 |  | 2.49 | Used for gyro mount
3 | Aluminum, 6061, 3/4"x 5", 1 ft | McMaster Carr | 8975K49 | 1 | 34.70 |  | 34.7
4 | carbon steel, disk, 1/8" th, 3.54" OD | 2TwentyTwo Steel Designs | --- | 2 | 2.12 |  | 4.24 | Simple reaction wheels
5 | Aluminum, 6061, 3/4"x3/4"x 1 ft | McMaster Carr | 9008K12 | 1 | 5.74 |  | 5.74 | Used for motor mount block
6 | Acetal Resin Rod 5/16" diam | McMaster Carr | 8572K52 | 1 | 3.2 |  | 3.2 | Used for balancing tip
7 | Aluminum Tube, 3003, 5/16" OD x 1ft | McMaster Carr | 7237K33 | 1 | 3.14 |  | 3.14 | Body
 |  |  |  |  |  |  | 68.65

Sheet: Sheet2
Center Tube Mass Calculation
Material: | 3003 Aluminum
Length: | 12 | in
Wall th. | 0.016 | in
ID | 0.28 | in
density | 2.73 | g/cc
volume | 0.178542994 | in3
volume | 2.925795464 | cc
mass | 7.987421618 | g

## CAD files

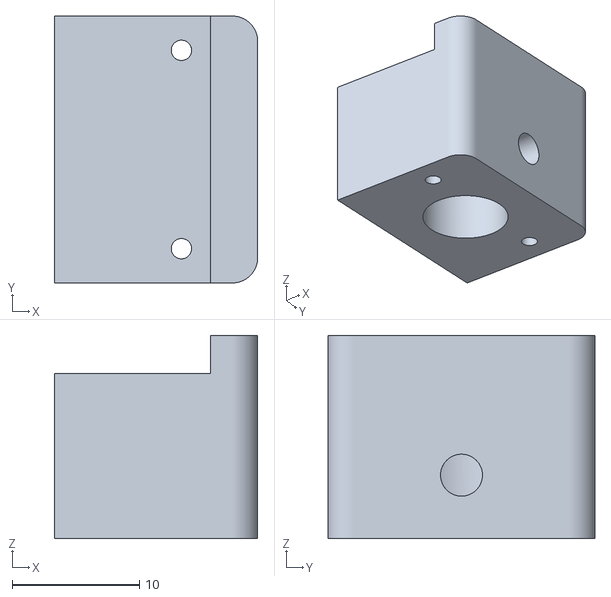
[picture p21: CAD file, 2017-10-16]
hardware/3D printer files/topBlock.stl
16.0 x 21.0 x 16.0

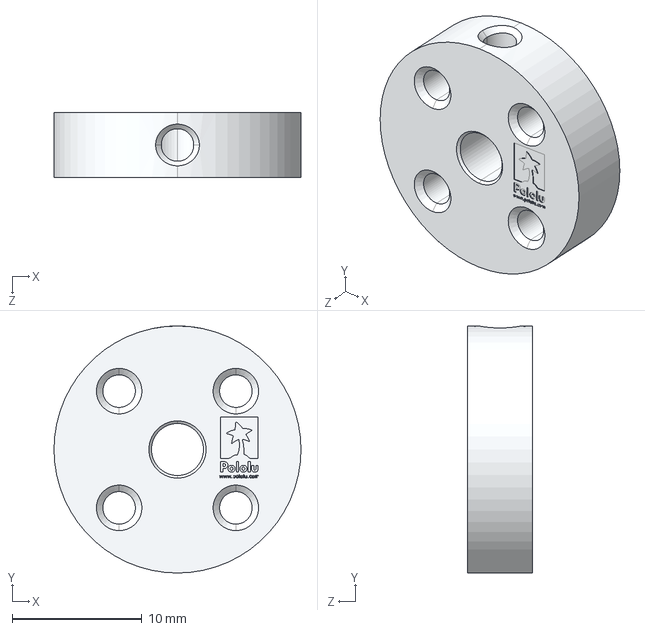
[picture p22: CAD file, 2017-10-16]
references/motor_hubs/pololu-universal-aluminum-mounting-hub-for-4mm-shaft-m3-holes.step
19.0 x 19.0 x 5.00 mm

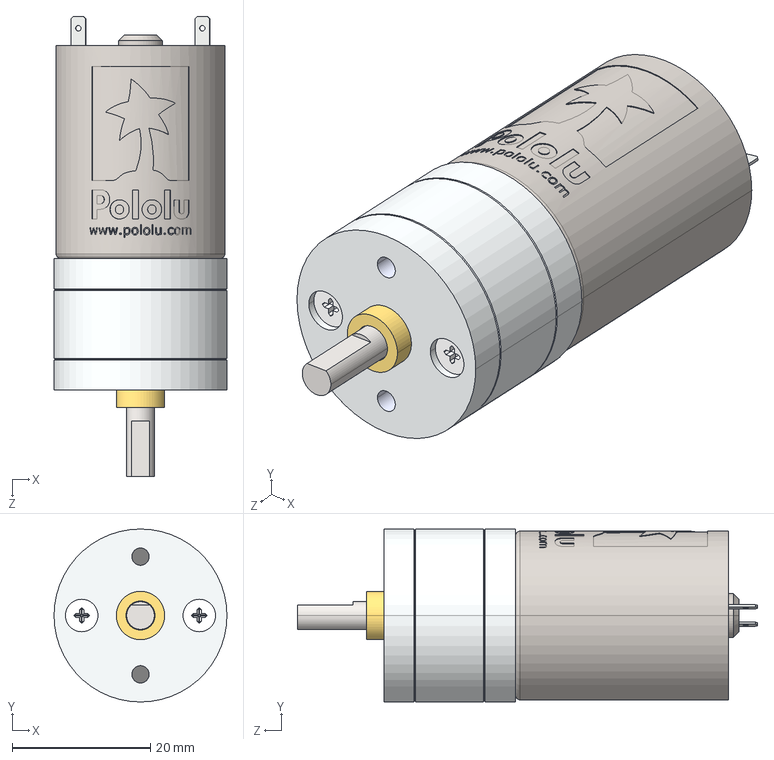
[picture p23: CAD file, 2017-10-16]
references/motors/25d-gearmotor-3d-models/25d-metal-gearmotor-20.4.step
25.0 x 25.0 x 66.5 mm

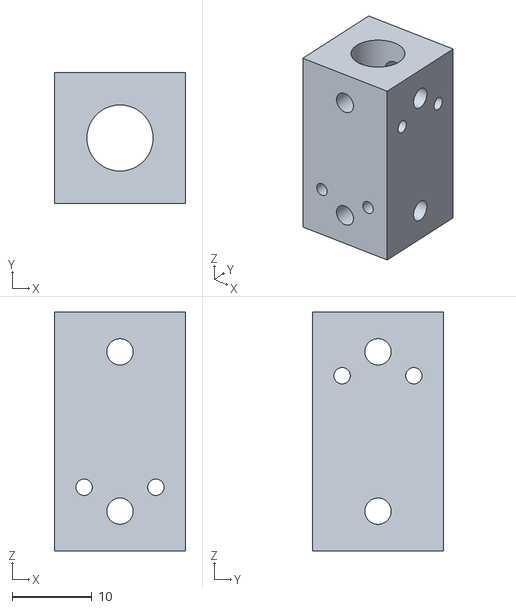
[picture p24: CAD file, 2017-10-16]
hardware/3D printer files/centerBlock.stl
16.5 x 16.5 x 30.0

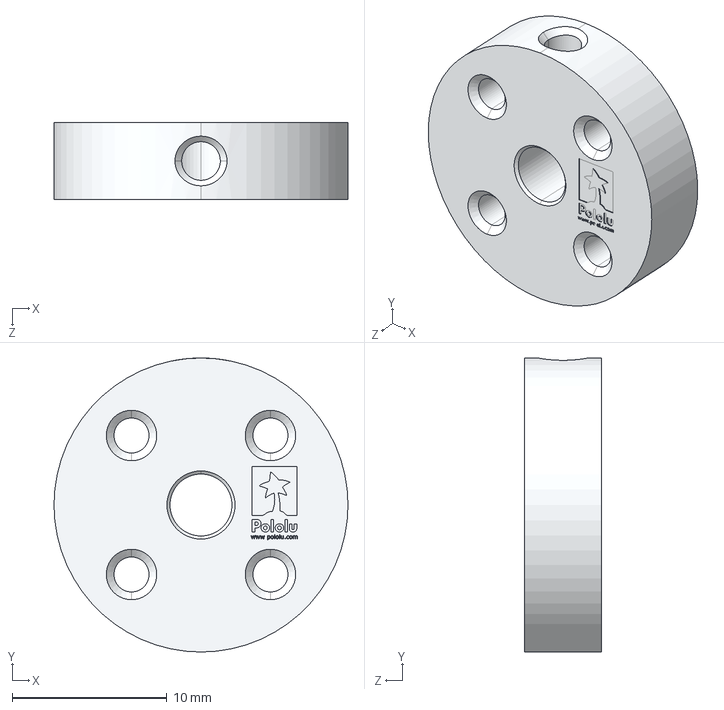
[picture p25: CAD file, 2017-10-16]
references/motor_hubs/pololu-universal-aluminum-mounting-hub-for-4mm-shaft-4-40-holes.step
19.0 x 19.0 x 5.00 mm

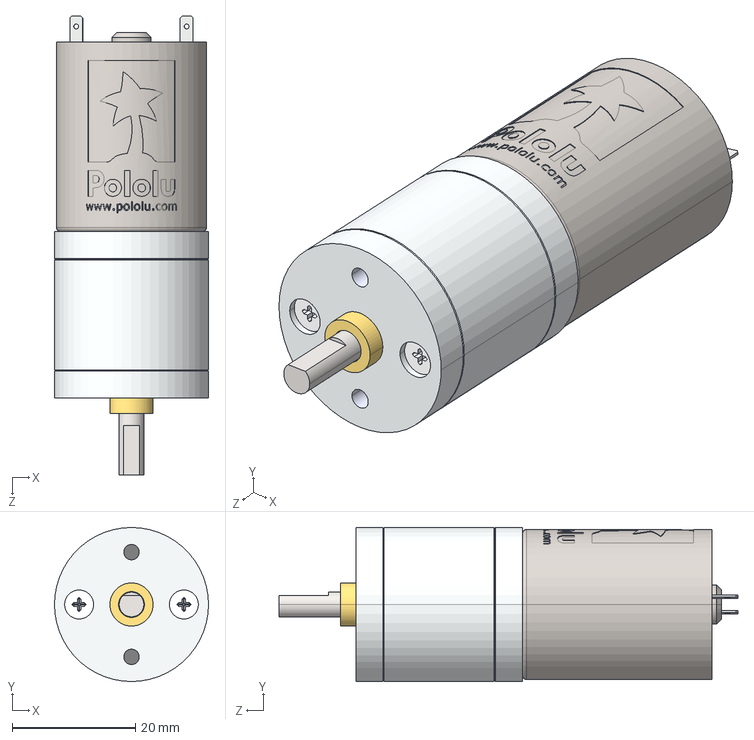
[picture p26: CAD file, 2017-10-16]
references/motors/25d-gearmotor-3d-models/25d-metal-gearmotor-378-499.step
25.0 x 25.0 x 74.5 mm

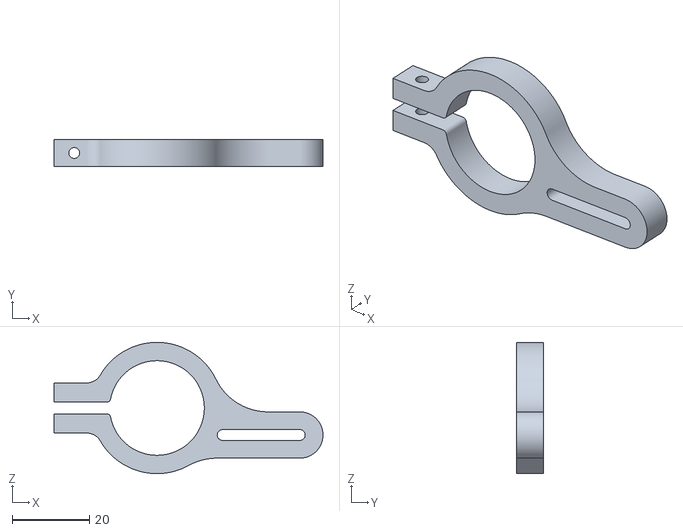
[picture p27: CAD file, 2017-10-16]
hardware/3D printer files/motorClip.stl
69.7 x 7.00 x 34.0

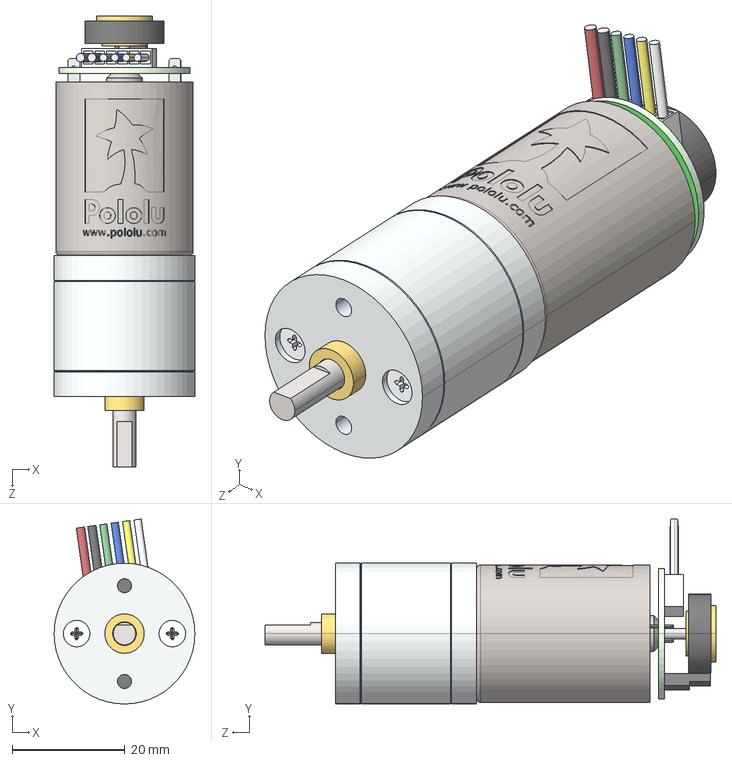
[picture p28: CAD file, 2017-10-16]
references/motors/25d-gearmotor-3d-models/25d-metal-gearmotor-172-227-encoder.step
25.0 x 32.9 x 80.0 mm

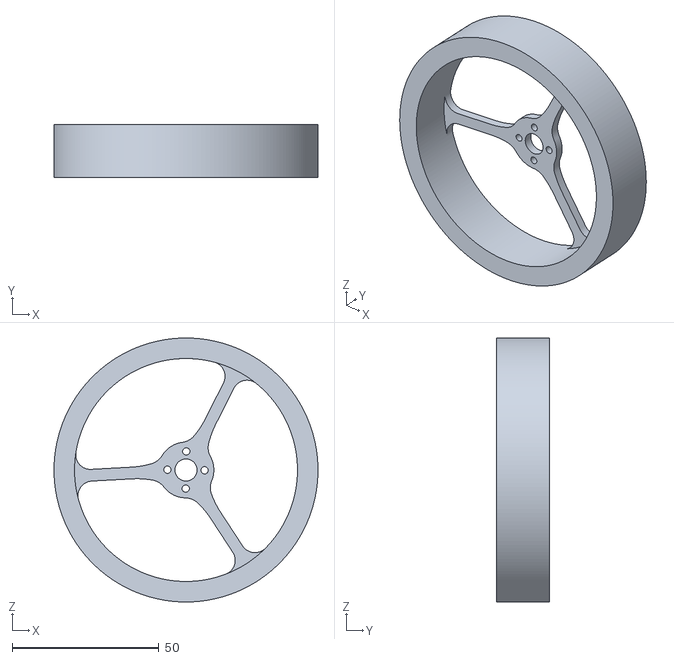
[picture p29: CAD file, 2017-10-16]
hardware/3D printer files/wheel.stl
90.0 x 18.0 x 90.0

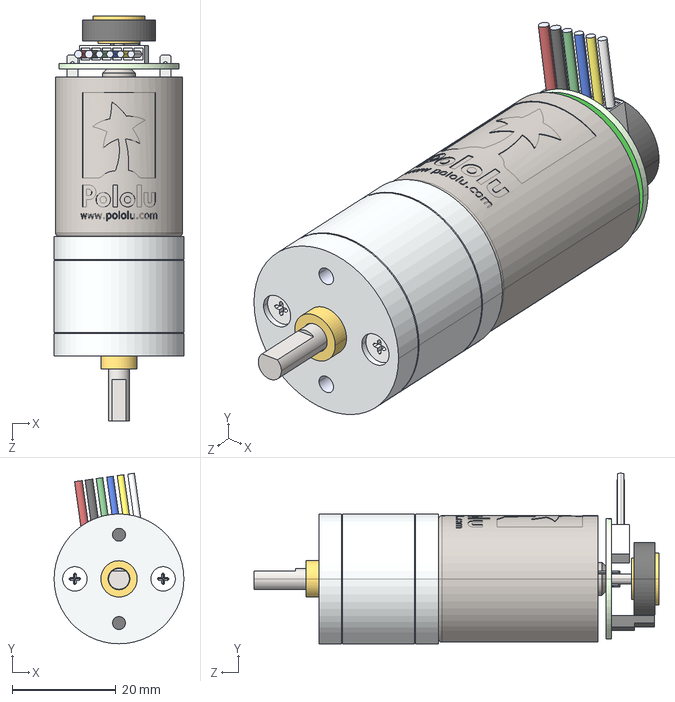
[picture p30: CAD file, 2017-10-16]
references/motors/25d-gearmotor-3d-models/25d-metal-gearmotor-75-99-encoder.step
25.0 x 32.9 x 78.0 mm

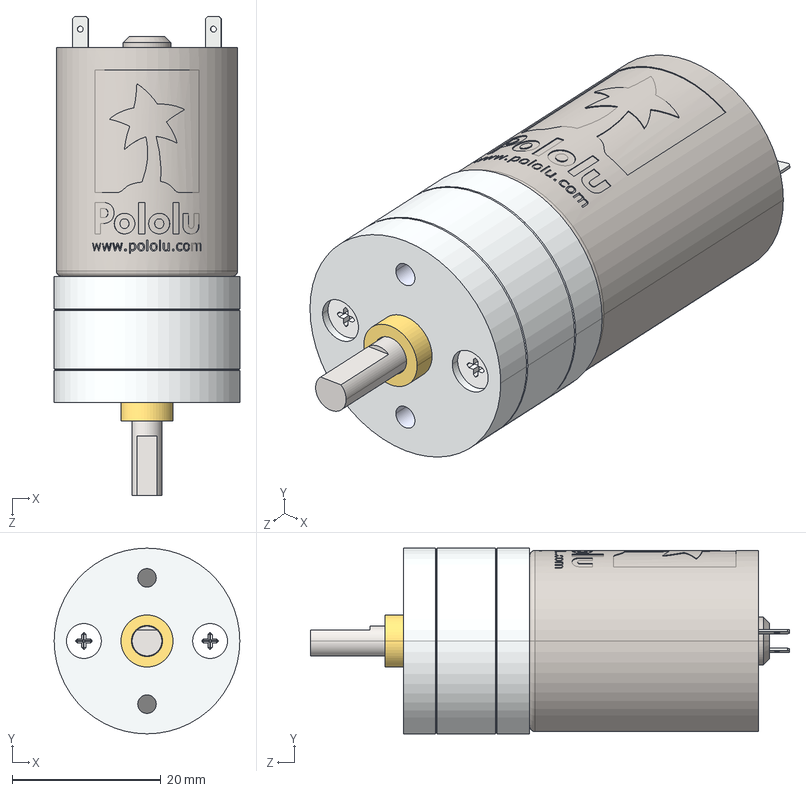
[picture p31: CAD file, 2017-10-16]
references/motors/25d-gearmotor-3d-models/25d-gearmotor-4.4-9.7.step
25.0 x 25.0 x 64.5 mm

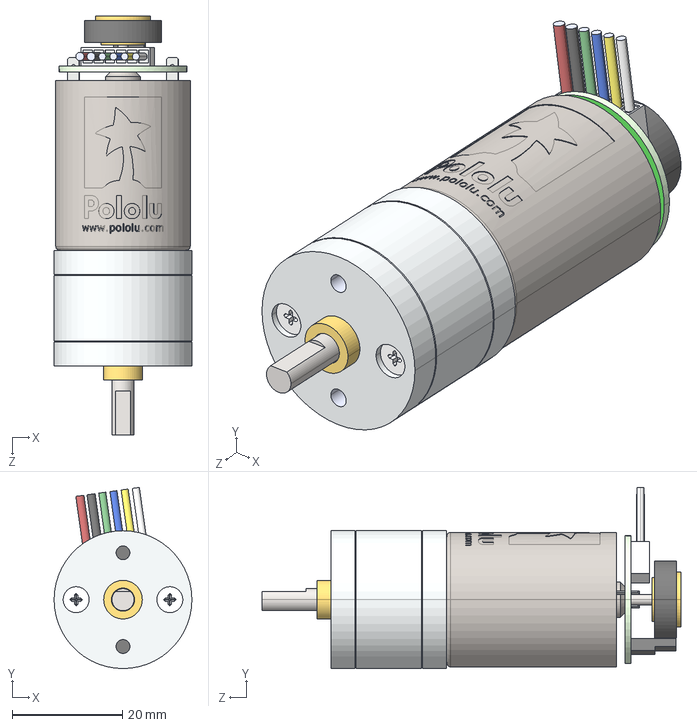
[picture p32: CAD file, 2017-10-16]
references/motors/25d-gearmotor-3d-models/25d-metal-gearmotor-34-47-encoder.step
25.0 x 32.9 x 76.0 mm

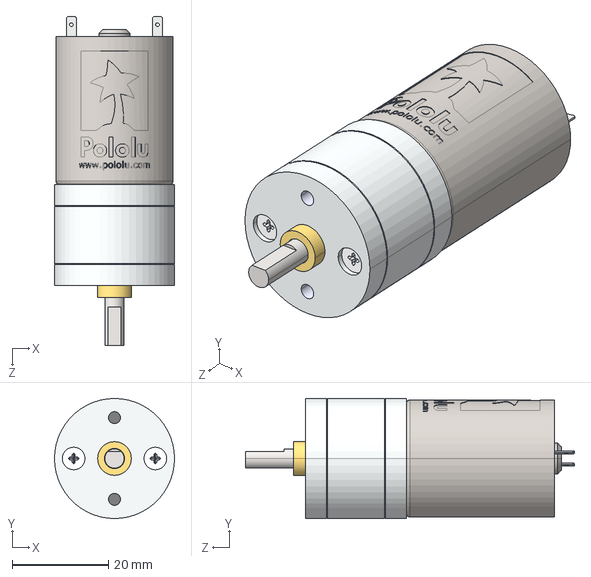
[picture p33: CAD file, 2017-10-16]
references/motors/25d-gearmotor-3d-models/25d-metal-gearmotor-34-47.step
25.0 x 25.0 x 68.5 mm

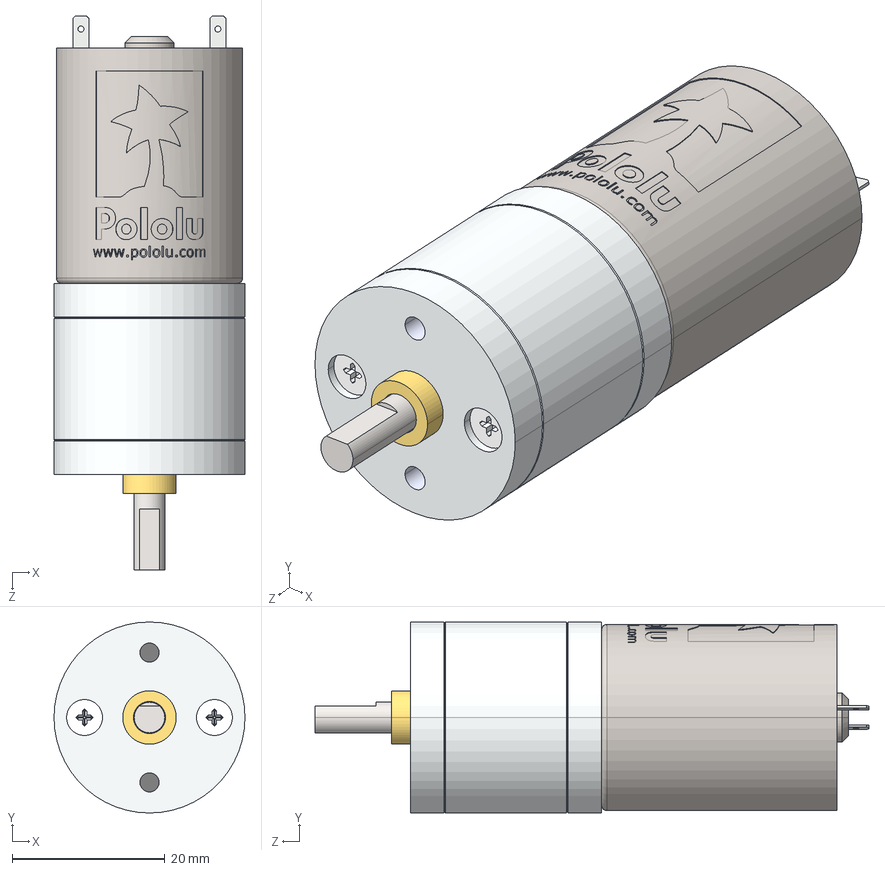
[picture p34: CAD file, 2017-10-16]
references/motors/25d-gearmotor-3d-models/25d-metal-gearmotor-172-227.step
25.0 x 25.0 x 72.5 mm

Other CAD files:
references/motors/25d-gearmotor-3d-models/25d-metal-gearmotor-4.4-9.7-encoder.step
references/motors/25d-gearmotor-3d-models/25d-metal-gearmotor-20.4-encoder.step
references/motors/25d-gearmotor-3d-models/25d-metal-gearmotor-378-499-encoder.step
references/motors/25d-gearmotor-3d-models/25d-metal-gearmotor-75-99.step

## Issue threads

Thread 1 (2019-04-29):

Arduino Code

Tomtom93, 2019-04-29:
Hello Alan,

I currently working on the Inverted Pendulum Reaction Wheel Project but I have few issues to fix like fix the PID gains for the controller.
First, did you use Pololu or Mitsumi motor in your code "Controller 3.0" ?
How did you calculate theta Kp, Kd and Ki and omega Kp, Kd and Ki ? What is theta and omega Ks, Kt and Kd ?
In fact, I have made a matlab model but I only have PID gains for the entire system..

Thank you for your time and thanks for reply.

Thomas R

AlanFord, 2019-04-29:
Hey Thomas,
You may be further along than I am - this is still a work in progress.  I had to teach myself control systems theory to figure out if the system would work with the parts I could find.  I'm now learning CNC to machine the components I need.  The code in Controller 3.0 is mostly the original Mike Rouleau code designed for the Mitsumi motors.  I'm using Pololu 25D 4:1 motors.  The derivation of the "K's" for my soon-to-be system can be found in the file latex/writeup-new.pdf.  I haven't looked at it in a while, but it looks like  theta Kp=266, theta Kd=1/4.5, and omega Kp=0.075.  Doesn't look like it needs the other constants.  (My notation is the pdf is a little sloppy - I'm still new to the control theory thing.) These constants are tied to the motor properties.  Also, the friction factor for my motors are different as they are geared motors - both the coulomb and viscous friction are significant (Appendix D of the pdf).  But in summary - Mike said he just adjusted the feedback constants by hand - impressive!

Tomtom93, 2019-04-29:
Ok thank you very much.
Does the program Controller 3.0 works with your Pololu motors
?

AlanFord, 2019-04-30:
They work with the motors.  Balancing will be tested when I get the reaction wheels fabricated.

Tomtom93, 2019-05-02:
Thank you for the clarification.

Have a good day,

Thomas.

Le mar. 30 avr. 2019 à 17:34, Alan Ford <notifications@github.com> a écrit :

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

simonbogh, 2019-10-07:
Hi @AlanFord

Did you get your project to work, does it balance? 😊 Thinking of building one myself.

Closed 2020-01-22.

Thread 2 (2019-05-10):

Program does'nt work properly

dhiamaulana, 2019-05-10:
Hallo, I am a student from Indonesia. I would like to inquire about this program that can not run properly on my Arduino IDE. **expected id-expression before '==' token** In one of the coding _5_interrupts, what should i do? Thanks sir

AlanFord, 2019-05-29:
I don't  seem to have the same problem - could it be that we are using different versions of the Arduino IDE?  I'm working with Arduino 1.8.7.  I'm working on a Mac, but that shouldn't make a difference.

dhiamaulana, 2019-06-20:
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
here's the problem i have been asked to you, sir. I don't know, what's word i change or added on your programs, cause every single act to create some new program on interrupt at the top of the programs, it doesn't work. Thank's sir for your respond

AlanFord, 2019-06-22:
It could be a couple of things.  (Sorry if you know all these things already - it may be new to some people.) First, the *.ino files are compiled in alphabetical order, so the Setup file (where PCintPort is declared) must be named so it is compiled before the Interrupts file.  Hence the file names _3_Setup.ino and _5_Interrupts.ino.  Changing the file names can break the compilation sequence.

It may also be that you need to install the PinChangeInt library.  This is different from the library found in the Arduino standard libraries.  The PinChangeInt library is found at https://github.com/GreyGnome/PinChangeInt

I hope this helps!

dhiamaulana, 2019-06-23:
Ok, Sir. Thanks a lot for the help. I'll learn from your code and your project's greater than any project i have been seeing, i'm watching your next project, sir. Sorry for bother you all time to help me :D

Closed 2019-06-23.

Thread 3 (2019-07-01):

Ask about using anohther motor DC

illgetmyluck, 2019-07-01:
can i use High Speed Motor DC 25GA370 12V 1000RPM w/ Encoder to change your pololu motor? Thanks

AlanFord, 2019-07-02:
It should work.  If you begin to approach the maximum RPM when balancing, you may wish to use slightly heavier reaction wheels.

illgetmyluck, 2019-07-09:
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

what should I wiring on arduino to change your pinout from pololu motor to arduino board? On your wiring picture, there's ' encoder ' and ' encoder interrupt ' it's same, mister? Sorry about asking you many question. Thanks Mister Alan

illgetmyluck, 2019-07-11:
what's meaning wire of current - L and current - R . Sorry mister, I didn't know how to wiring that red sign of current. Thanks

AlanFord, 2020-01-22:
> what should I wiring on arduino to change your pinout from pololu motor to arduino board? On your wiring picture, there's ' encoder ' and ' encoder interrupt ' it's same, mister? Sorry about asking you many question. Thanks Mister Alan

Most encoders have two phases and each will generate signals when they change states (between high and low).  It's best to assign a software interrupt to both - you get the most accurate sensing of the motor position.  Unfortunately, the Arduino Uno only supports two interrupts that can be triggered by an external sensor; these interrupts are tied to Digitial Pins 2 and 3.  Thus, one phase of each motor is connected to either Digital Pin 2 or Digital Pin 3. The second phase of each encoder is then connected to any available input pin.  In your figure Encoder Interrupt would be Encoder A Phase from each motor, connected to either Pin 2 or 3.  The Encoder (B) is the B Phase connection from each motor, connected to Arduino pins A2 and digital 4.

AlanFord, 2020-01-22:
Current - L and Current - R would be connected if the Arduino is being used to directly measure the current supplied to the left and right motors, respectively.  Some motor controllers support this function, although I've found it generally not accurate enough to used in the feedback control loop.

Closed 2022-02-19.

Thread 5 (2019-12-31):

arduino code possible issue

dtaminge, 2019-12-31:
Hi all, I am working on creating this project as just a cool project to pass time, but I am having tones of issues. I was wondering if someone could send me a copy of their code for me to use as an example, because I honestly have no clue what variables in the global variables page we are supposed to update (I assume that they should not all equal zero). I believe that I have all of my wiring correct as well, but I just cannot get anything to happen. Also do we need to use the 4a motor control board for this to work?
Thanks

AlanFord, 2020-01-19:
If you hook up the Arduino IDE serial monitor you should be able to communicate with the controller and set quite a number of parameters.  It looks like Mike Rouleau originally intended to use potentiometers connected to the Arduino to adjust the parameters, but then switched to a serial interface.  To use a different motor control board, adjust the pin definitions in Controller_3.0.ino to match the motor control board that you intend to use.

dtaminge, 2020-01-19:
> If you hook up the Arduino IDE serial monitor you should be able to communicate with the controller and set quite a number of parameters. It looks like Mike Rouleau originally intended to use potentiometers connected to the Arduino to adjust the parameters, but then switched to a serial interface. To use a different motor control board, adjust the pin definitions in Controller_3.0.ino to match the motor control board that you intend to use.

Thanks for getting back to me. I got things communicating, but for some reason I have to just set stat equal to a value instead of allowing it to fluctuate. On top of that the arduino crashes after 30 seconds from an overflow of data

AlanFord, 2020-01-26:
Ok, I'm starting to take Mike's code apart and see where there may be a bug.  I don't see a crash from an overflow of data.  My past experience with other projects would indicate that the code isn't handling interrupts fast enough and they over-run each other, causing a lockup.  Try disabling your motors and encoders and see if crash continues.  Without the encoders, the encoder interrupts shouldn't fire.  If they still do, check for input noise on the encoder pins or proper pin assignment.

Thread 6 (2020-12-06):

I reported an error when compiling the project

rose387, 2020-12-06:
Hi，all，When I compile the project in arduino, I get an error，How to obtain the libraries referenced by these two header files   #include <PinChangeInt.h> #include <digitalWriteFast.h>
Arduino:1.8.13 (Windows 10), 开发板："Arduino Uno"

Controller_3.0:65:10: fatal error: PinChangeInt.h: No such file or directory

compilation terminated.

exit status 1

PinChangeInt.h: No such file or directory

在文件 -> 首选项开启
“编译过程中显示详细输出”选项
这份报告会包含更多信息。

rose387, 2020-12-06:
I have solved this problem，

Closed 2022-02-14.

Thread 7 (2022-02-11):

Serial Monitor showing blank

schakra42, 2022-02-11:
when running the Arduino code, it compiles and uploads correctly but the serial monitor is completely blank and there is no response from the system even with the correct Baud rate. Do you have any insight on what might be the issue?

AlanFord, 2022-02-13:
I haven't worked with the Arduino code in a while, but I will retrieve an Arduino from the local hackerspace and try it out.  Usually it's an incorrect baud rate, but I think you have that sorted.  Another possibility would be some other software attempting to use the same usb/serial port.  Lastly, some boards will appear to hang-up if there is no device (in this case, the gyro) attached to the I2C port.  In reality they are just waiting to time-out during the I2C initialization.  In any event, I'll try the software out and get back to you.

AlanFord, 2022-02-14:
I can confirm there is a problem.  I tested with an Arduino UNO R3 board, Arduino 1.8.18 IDE, and CoolTerm as a serial terminal.  I dropped the baud rate to 19200 to avoid over-stressing anything.  I added a simple print statement following "Serial.begin(serial_Frequency);" in setup().  I can get three characters out of the serial connection before it stops.  I suspect that something has changed in the Arduino core libraries that is conflicting with the program.  I will add it to my todo list.

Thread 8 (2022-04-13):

Arduino Compiling error

antoniohof, 2022-04-13:
Dear Alan,

My arduino code is trowing this error:

no 'uint8_t MPU6050_Base::dmpInitialize()' member function declared in class 'MPU6050_Base'

Do you happen to know something about it?
 I think its a conflict between libraries maybe.

Thanks for the amazing. project

Antonio

antoniohof, 2022-04-13:
In file included from /Users/antoniohof/Projects/Caneta/NEW-TEST/firmware/Arduino/Controller_3.0/Controller_3.0.ino:9:0:
MPU6050_6Axis_MotionApps20_mod_1.h:325:32: error: no 'uint8_t MPU6050_Base::dmpInitialize()' member function declared in class 'MPU6050_Base'
 uint8_t MPU6050::dmpInitialize() {

antoniohof, 2022-04-13:
I found that the newest i2c has this problem. so I used this version:
https://github.com/jrowberg/i2cdevlib/tree/490c9c68cc0f0b73e5c8a3d9bb569a44f278ff60

Closed 2022-04-13.

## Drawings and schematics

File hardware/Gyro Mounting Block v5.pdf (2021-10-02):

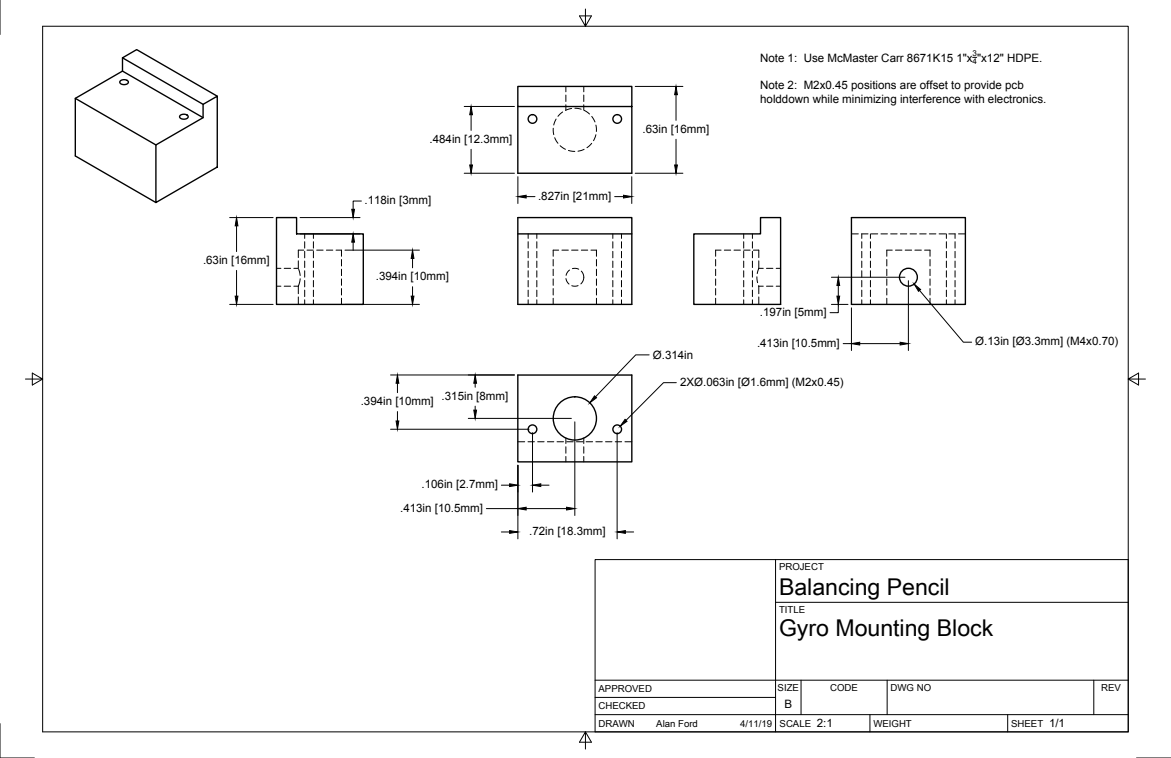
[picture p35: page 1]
SIZE; CODE; DWG NO; REV; Alan Ford; 3/4"x12" HDPE.

Note 1: Use McMaster Carr 8671K15 1"x

Note 2: M2x0.45 positions are offset to provide pcb
holddown while minimizing interference with electronics.

PROJECT
Balancing Pencil
Gyro Mounting Block

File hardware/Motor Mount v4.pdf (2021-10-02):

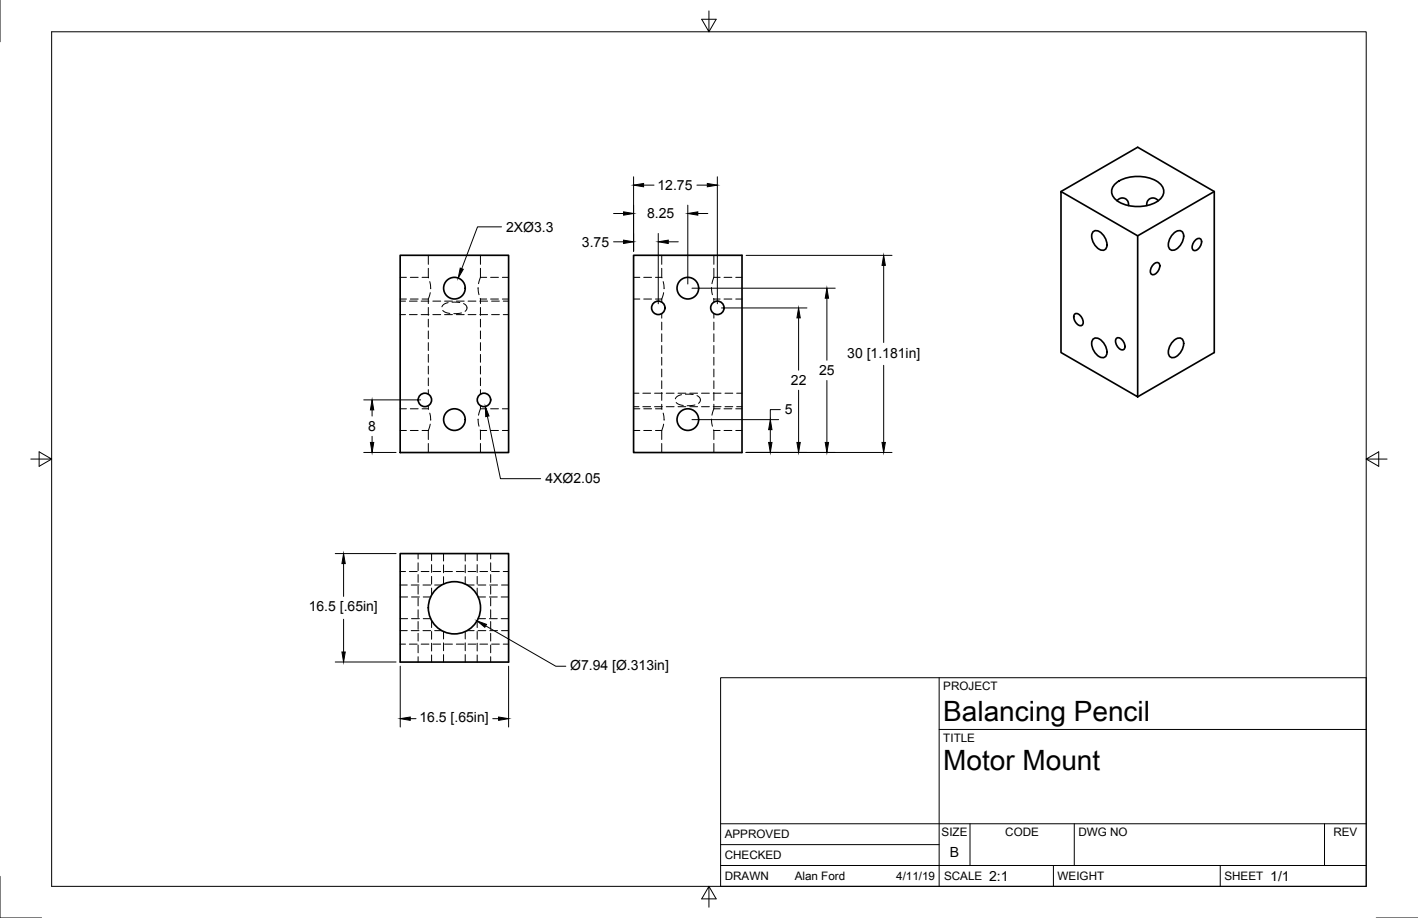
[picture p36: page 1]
SIZE; CODE; DWG NO; REV; Alan Ford; Balancing Pencil; Motor Mount

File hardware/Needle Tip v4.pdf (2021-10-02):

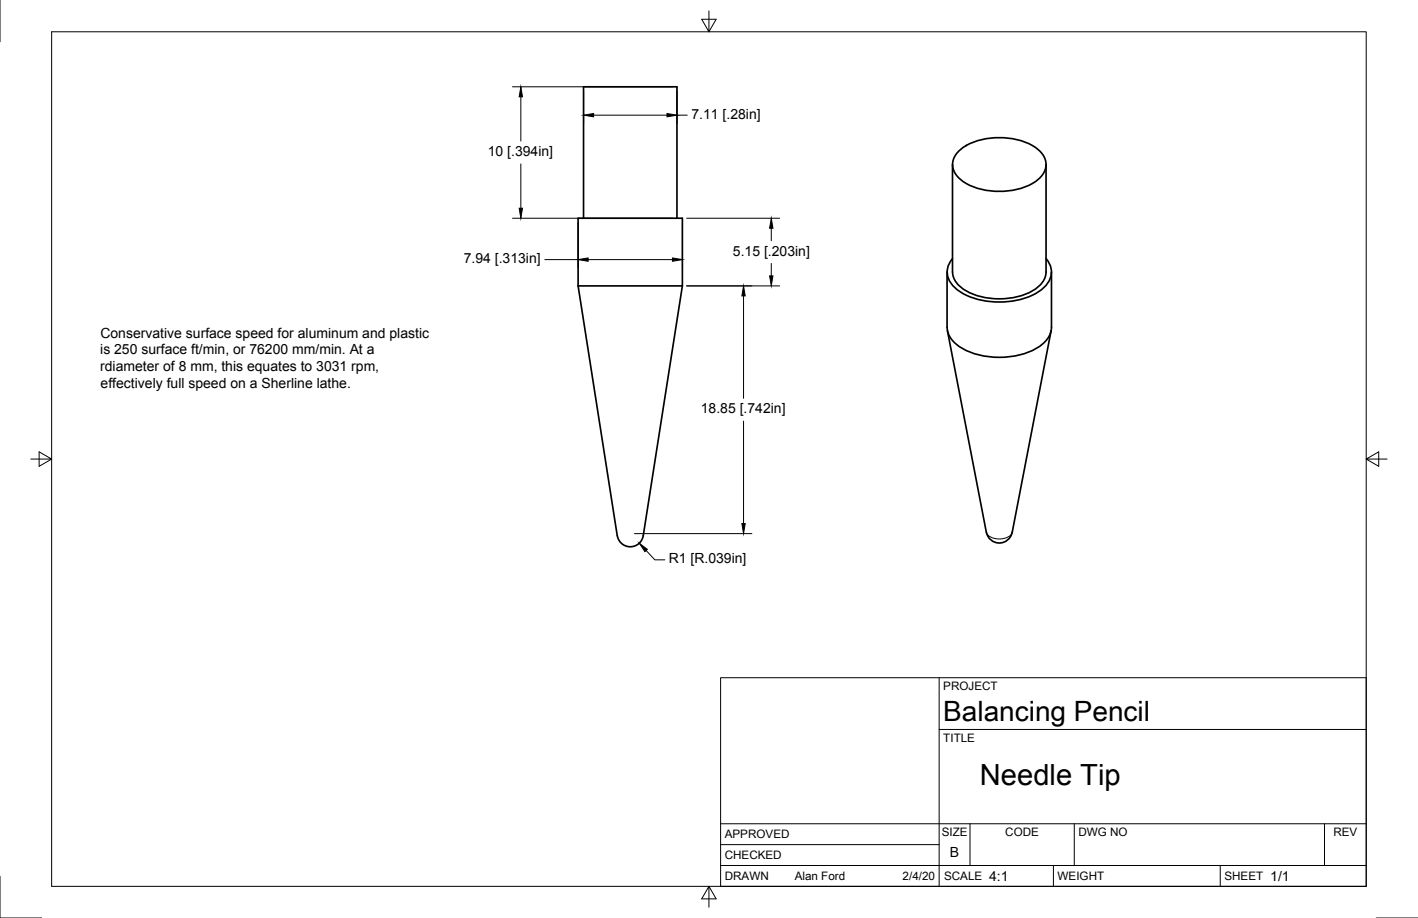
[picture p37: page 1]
SIZE; CODE; DWG NO; REV; Alan Ford; Balancing Pencil; Needle Tip

Conservative surface speed for aluminum and plastic
is 250 surface ft/min, or 76200 mm/min. At a
rdiameter of 8 mm, this equates to 3031 rpm,
effectively full speed on a Sherline lathe.

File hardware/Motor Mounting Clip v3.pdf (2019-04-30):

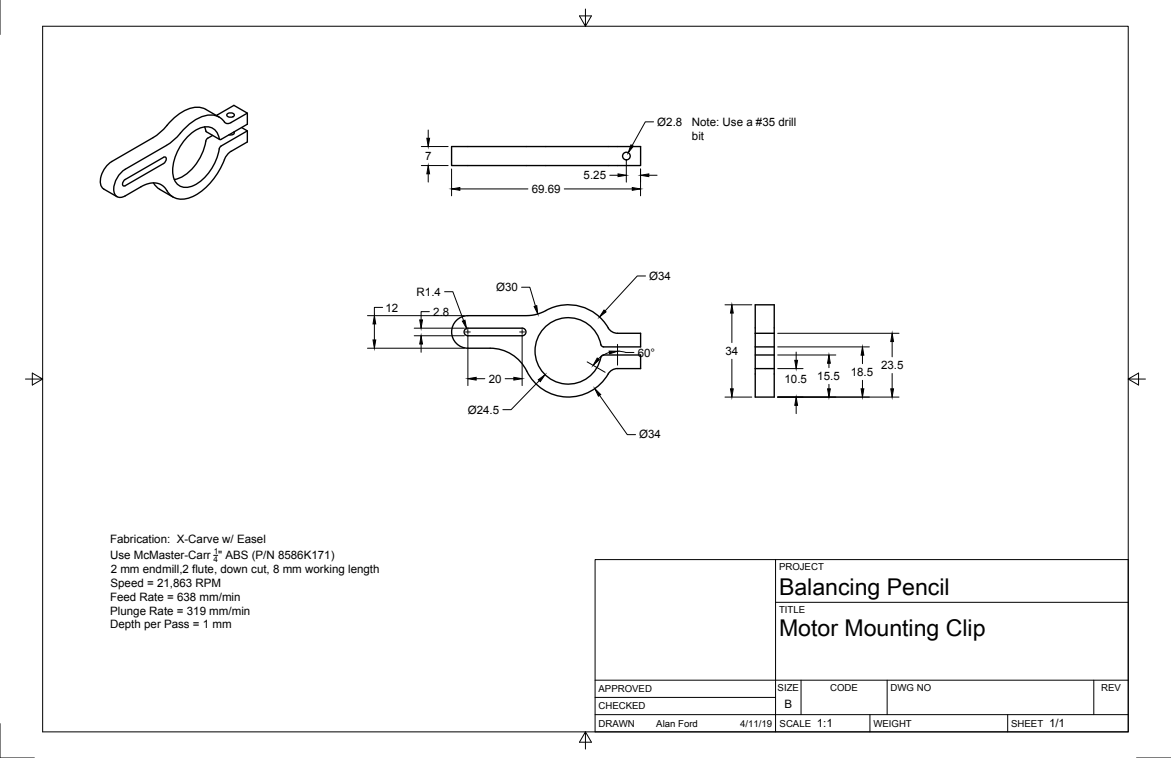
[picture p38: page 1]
SIZE; CODE; DWG NO; REV; Alan Ford; " ABS (P/N 8586K171)

Note: Use a #35 drill
bit

Fabrication: X-Carve w/ Easel
Use McMaster-Carr 1
2 mm endmill,2 flute, down cut, 8 mm working length
Speed = 21,863 RPM
Feed Rate = 638 mm/min
Plunge Rate = 319 mm/min
Depth per Pass = 1 mm

PROJECT
Balancing Pencil
Motor Mounting Clip

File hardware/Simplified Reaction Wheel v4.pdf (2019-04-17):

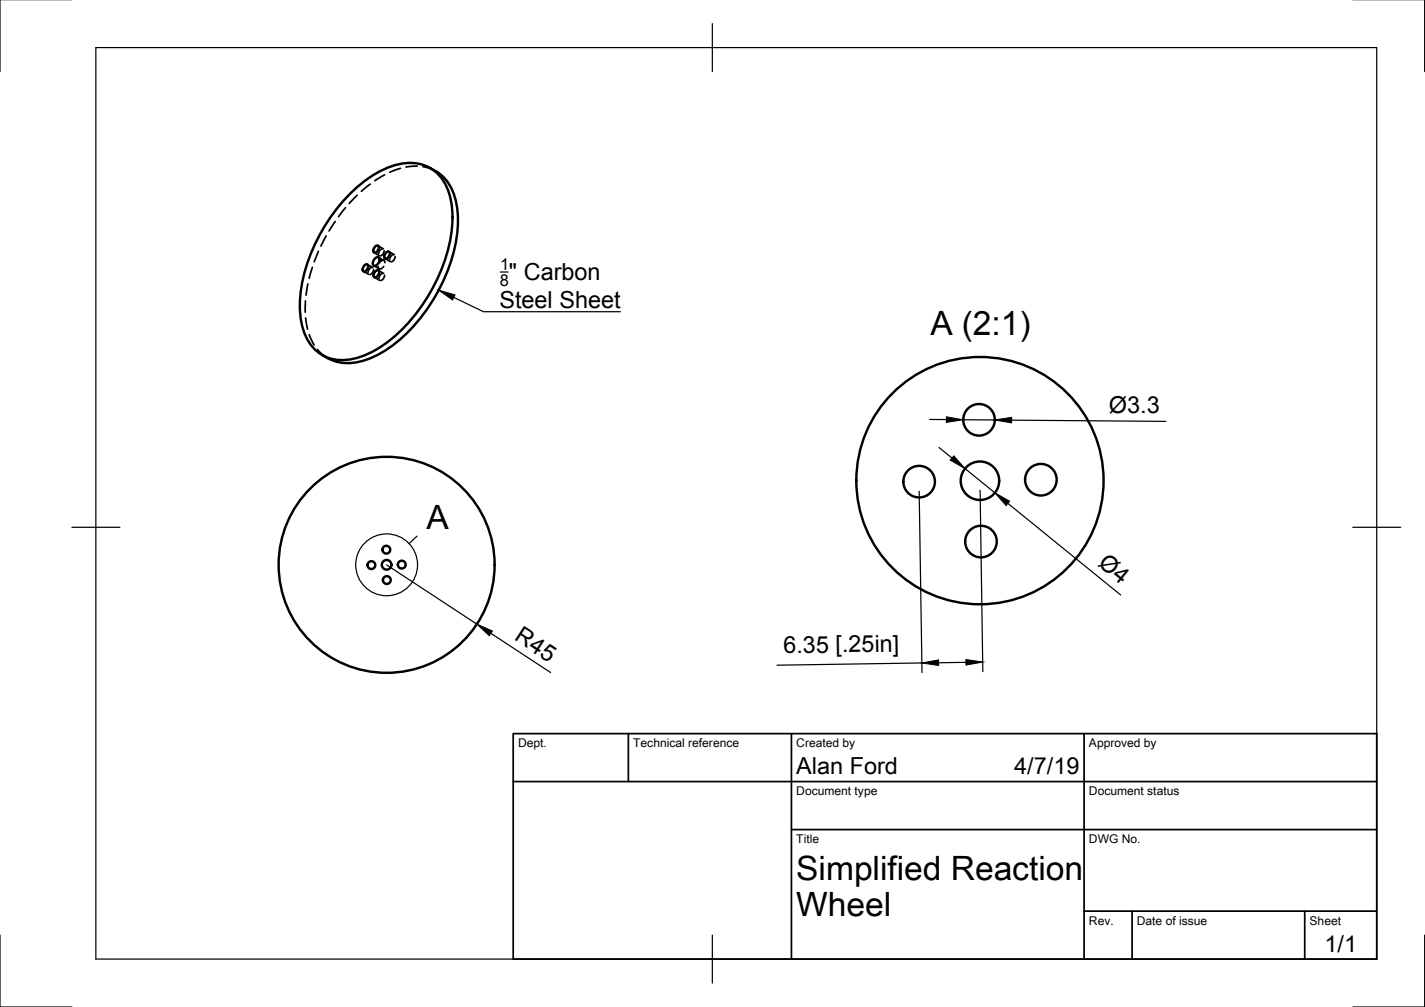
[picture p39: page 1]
1/8" Carbon Steel Sheet

Dept. | Technical reference | Created by Alan Ford 4/7/19 | Approved by

Document type | Document status

Title Simplified Reaction Wheel | DWG No.

Rev. | Date of issue | Sheet 1/1

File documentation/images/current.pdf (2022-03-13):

## Current vs RPM

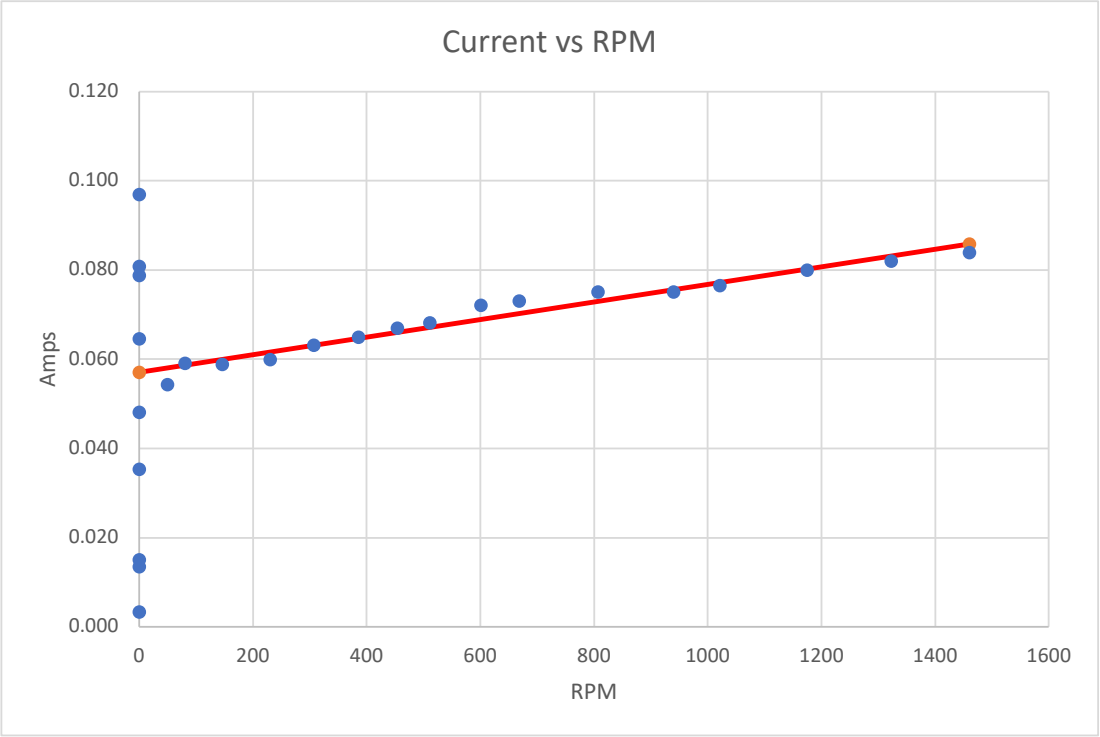
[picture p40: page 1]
Amps; RPM

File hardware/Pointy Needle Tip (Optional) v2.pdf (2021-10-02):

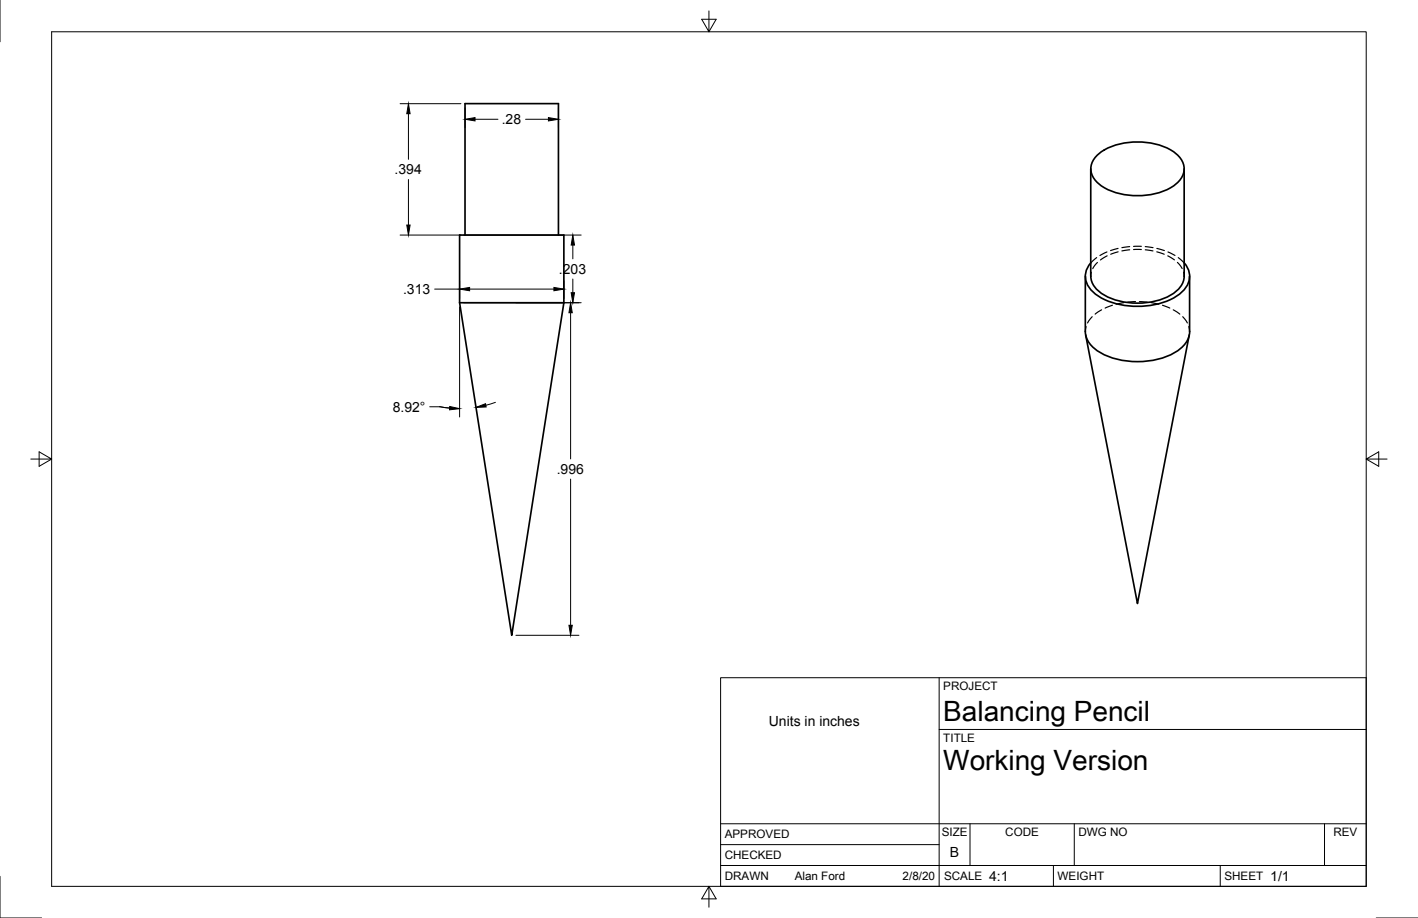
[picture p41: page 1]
SIZE; CODE; DWG NO; REV; Alan Ford; Balancing Pencil; Working Version

Units in inches

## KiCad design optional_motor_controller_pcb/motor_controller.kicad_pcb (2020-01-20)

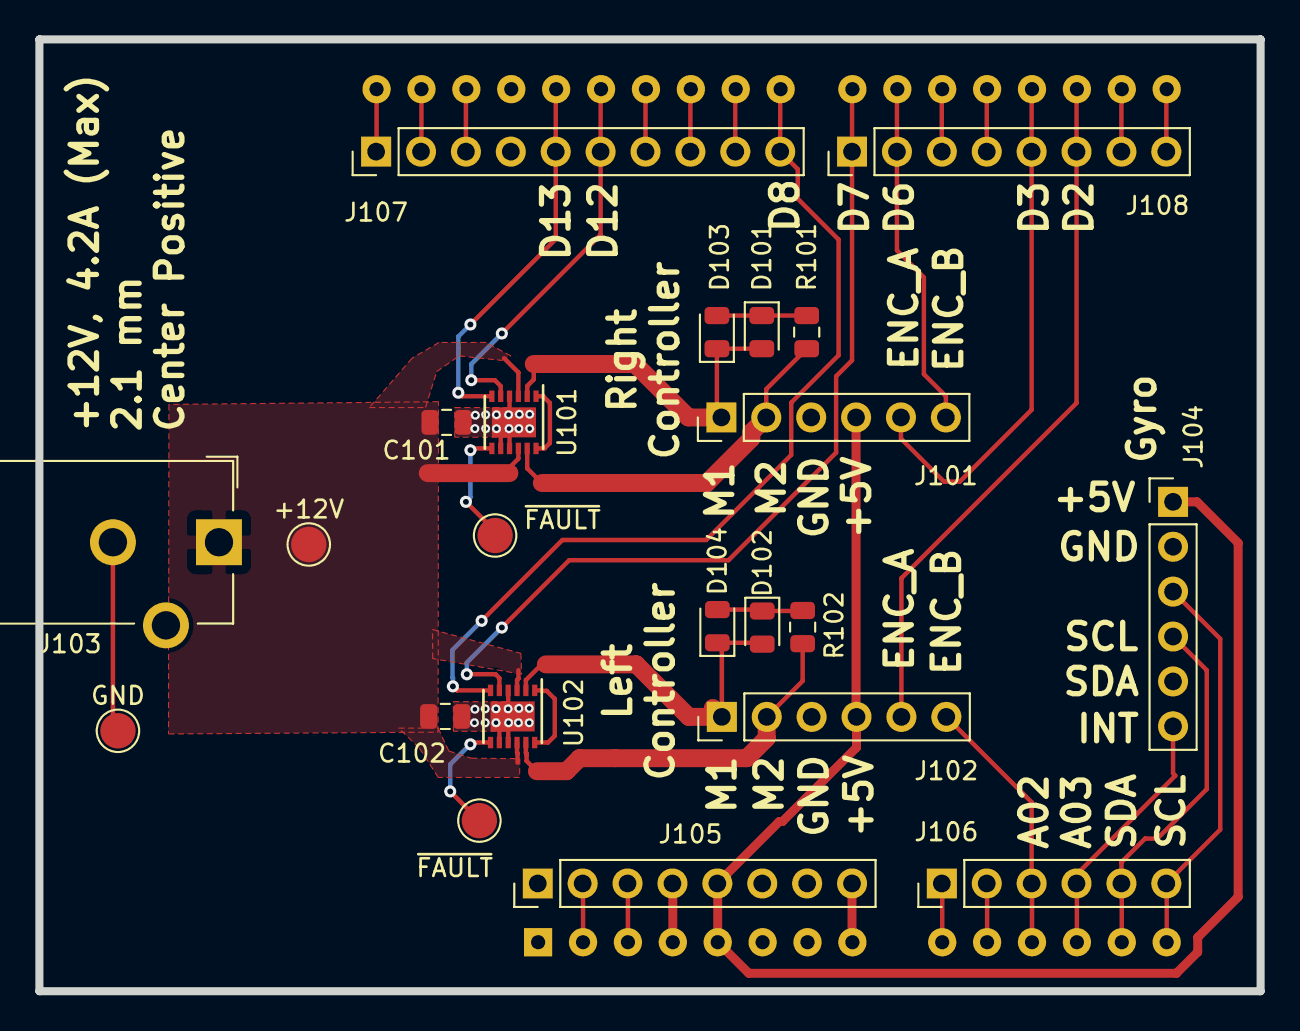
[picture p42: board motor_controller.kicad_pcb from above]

Board: 2 copper layers, 69.1 x 53.8 mm, 21 parts (1 on the bottom side), 38 nets.

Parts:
+12V: TestPoint_Pad_D2.0mm
A101: Arduino_UNO_R3
C101, C102: 1 uF; C_0805_2012Metric
D101, D102: RED; LED_0805_2012Metric
D103, D104: GREEN; LED_0805_2012Metric
GND: TestPoint_Pad_D2.0mm
J101, J102, J104, J106: Conn_01x06; PinHeader_1x06_P2.54mm_Vertical
J103: Barrel_Jack_Switch; BarrelJack_CUI_PJ-102AH_Horizontal
J105, J108: Conn_01x08; PinHeader_1x08_P2.54mm_Vertical
J107: Conn_01x10; PinHeader_1x10_P2.54mm_Vertical
R101, R102: 4.7K; R_0805_2012Metric
U101, U102: MAX14780; max14870

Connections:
+3V3: A101.4, J105.4
+5V: A101.5, J101.4, J102.4, J104.1, J105.5
+12V: +12V.1, C101.1, C102.1, J103.1, U101.3, U101.10, U102.3, U102.10
/A0: A101.9, J106.1
/A1: A101.10, J106.2
/A2: A101.11, J102.6, J106.3
/A3: A101.12, J104.6, J106.4
/ALT_SCL: A101.32, J107.1
/ALT_SDA: A101.31, J107.2
/AREF: A101.30, J107.3
/D0: A101.15, J108.8
/D1: A101.16, J108.7
/D2: A101.17, J102.5, J108.6
/D3: A101.18, J101.5, J108.5
/D4: A101.19, J108.4
/D5: A101.20, J108.3
/D6: A101.21, J101.6, J108.2
/D7: A101.22, J108.1, U102.5
/D8: A101.23, J107.10, U102.6
/D9: A101.24, J107.9
/D10: A101.25, J107.8
/D11: A101.26, J107.7
/D12: A101.27, J107.6, U101.5
/D13: A101.28, J107.5, U101.6
/IOREF: A101.2, J105.2
/M1L: D102.2, D104.1, J102.1, U102.2
/M1R: D101.2, D103.1, J101.1, U101.2
/M2L: J102.2, R102.2, U102.11
/M2R: J101.2, R101.2, U101.11
/RESET: A101.3, J105.3
/SCL: A101.14, J104.3, J106.6
/SDA: A101.13, J104.4, J106.5
/Vin: A101.8, J105.8
GND: A101.6, A101.7, A101.29, C101.2, C102.2, GND.1, J101.3, J102.3, J103.2, J104.2, J105.6, J105.7, J107.4, U101.4, U101.8, U101.9, U101.13, U102.4, U102.8, U102.9, U102.13
unnamed: D101.1, D103.2, R101.1
unnamed: D102.1, D104.2, R102.1
unnamed: U101.1, U101.12
unnamed: U102.1, U102.12

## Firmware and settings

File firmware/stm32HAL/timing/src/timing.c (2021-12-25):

/*
 ============================================================================
 Name        : register.c
 Author      : 
 Version     :
 Copyright   : Your copyright notice
 Description : calculate STM32 I2C timing
               Derived from Arduino STM32 twi.c

  ******************************************************************************
  * @attention
  *
  * <h2><center>&copy; COPYRIGHT(c) 2016 STMicroelectronics</center></h2>
  *
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
  ******************************************************************************

 ============================================================================
 */

#include <stdio.h>
#include <stdlib.h>
uint32_t i2c_computeTiming(uint32_t clkSrcFreq, uint32_t i2c_speed);
#define I2C_VALID_TIMING_NBR          64U

/* Generic definition for series requiring I2C timing calculation */

#ifndef I2C_VALID_TIMING_NBR
#define I2C_VALID_TIMING_NBR          8U
#endif
#define I2C_ANALOG_FILTER_DELAY_MIN  50U /* ns */
#ifndef I2C_ANALOG_FILTER_DELAY_MAX
#define I2C_ANALOG_FILTER_DELAY_MAX 260U /* ns */
#endif
#ifndef I2C_USE_ANALOG_FILTER
#define I2C_USE_ANALOG_FILTER         1U
#endif
#ifndef I2C_DIGITAL_FILTER_COEF
#define I2C_DIGITAL_FILTER_COEF       0U
#endif
#define I2C_PRESC_MAX                16U
#define I2C_SCLDEL_MAX               16U
#define I2C_SDADEL_MAX               16U
#define I2C_SCLH_MAX                256U
#define I2C_SCLL_MAX                256U
#define SEC2NSEC            1000000000UL

typedef enum {
  I2C_SPEED_FREQ_STANDARD,  /* 100 kHz */
  I2C_SPEED_FREQ_FAST,      /* 400 kHz */
  I2C_SPEED_FREQ_FAST_PLUS, /* 1 MHz */
  I2C_SPEED_FREQ_NUMBER     /* Must be the last entry */
} I2C_speed_freq_t;

typedef struct {
  uint32_t input_clock;      /* I2C Input clock */
  uint32_t timing;           /* I2C timing corresponding to Input clock */
} I2C_timing_t;

static I2C_timing_t I2C_ClockTiming[I2C_SPEED_FREQ_NUMBER] = {0};

typedef struct {
  uint32_t freq;      /* Frequency in Hz */
  uint32_t freq_min;  /* Minimum frequency in Hz */
  uint32_t freq_max;  /* Maximum frequency in Hz */
  uint16_t hddat_min; /* Minimum data hold time in ns */
  uint16_t vddat_max; /* Maximum data valid time in ns */
  uint16_t sudat_min; /* Minimum data setup time in ns */
  uint16_t lscl_min;  /* Minimum low period of the SCL clock in ns */
  uint16_t hscl_min;  /* Minimum high period of SCL clock in ns */
  uint16_t trise;     /* Rise time in ns */
  uint16_t tfall;     /* Fall time in ns */
  uint8_t dnf;       /* Digital noise filter coefficient */
} I2C_Charac_t;

static const I2C_Charac_t I2C_Charac[] = {
  [I2C_SPEED_FREQ_STANDARD] =
  {
    .freq = 100000,
    .freq_min = 80000,
    .freq_max = 120000,
    .hddat_min = 0,
    .vddat_max = 3450,
    .sudat_min = 250,
    .lscl_min = 4700,
    .hscl_min = 4000,
    .trise = 640,
    .tfall = 20,
    .dnf = I2C_DIGITAL_FILTER_COEF,
  },
  [I2C_SPEED_FREQ_FAST] =
  {
    .freq = 400000,
    .freq_min = 320000,
    .freq_max = 480000,
    .hddat_min = 0,
    .vddat_max = 900,
    .sudat_min = 100,
    .lscl_min = 1300,
    .hscl_min = 600,
    .trise = 250,
    .tfall = 100,
    .dnf = I2C_DIGITAL_FILTER_COEF,
  },
  [I2C_SPEED_FREQ_FAST_PLUS] =
  {
    .freq = 1000000,
    .freq_min = 800000,
    .freq_max = 1200000,
    .hddat_min = 0,
    .vddat_max = 450,
    .sudat_min = 50,
    .lscl_min = 500,
    .hscl_min = 260,
    .trise = 60,
    .tfall = 100,
    .dnf = I2C_DIGITAL_FILTER_COEF,
  }
};

int main(void) {
	uint32_t ret = 0;
	puts("!!!Hello World!!!"); /* prints !!!Hello World!!! */
    ret = i2c_computeTiming(72000000, I2C_SPEED_FREQ_STANDARD);
    if (ret == 0xFFFFFFFF) {
    	printf("No valid configuration!\n");
    }
    else {
    	printf("I2C configuration = %i\n", ret);
    }
	return EXIT_SUCCESS;
}

/**
* @brief Calculate PRESC, SCLDEL, SDADEL, SCLL and SCLH and find best configuration.
* @param clkSrcFreq I2C source clock in HZ.
* @param i2c_speed I2C frequency (index).
* @retval config index (0 to I2C_VALID_TIMING_NBR], 0xFFFFFFFF for no
valid config.
*/
uint32_t i2c_computeTiming(uint32_t clkSrcFreq, uint32_t i2c_speed)
{
  uint32_t ret = 0xFFFFFFFFU;
  uint32_t valid_timing_nbr = 0;
  uint32_t ti2cclk;
  uint32_t ti2cspeed;
  uint32_t prev_error;
  uint32_t dnf_delay;
  uint32_t clk_min, clk_max;
  uint16_t scll, sclh;
  uint8_t prev_presc = I2C_PRESC_MAX;

  int32_t tsdadel_min, tsdadel_max;
  int32_t tscldel_min;
  uint8_t presc, scldel, sdadel;
  uint32_t tafdel_min, tafdel_max;

  if (i2c_speed < I2C_SPEED_FREQ_NUMBER) {

    /* Don't compute timing if already available value for the requested speed with the same I2C input frequency */
    if ((I2C_ClockTiming[i2c_speed].input_clock == clkSrcFreq) && (I2C_ClockTiming[i2c_speed].timing != 0U)) {
      ret = I2C_ClockTiming[i2c_speed].timing;
    } else {
      /* Save the I2C input clock for which the timing will be saved */
      I2C_ClockTiming[i2c_speed].input_clock = clkSrcFreq;

      ti2cclk = (SEC2NSEC + (clkSrcFreq / 2U)) / clkSrcFreq;
      ti2cspeed = (SEC2NSEC + (I2C_Charac[i2c_speed].freq / 2U)) / I2C_Charac[i2c_speed].freq;

      tafdel_min = (I2C_USE_ANALOG_FILTER == 1U) ? I2C_ANALOG_FILTER_DELAY_MIN : 0U;
      tafdel_max = (I2C_USE_ANALOG_FILTER == 1U) ? I2C_ANALOG_FILTER_DELAY_MAX : 0U;
      /*
       * tDNF = DNF x tI2CCLK
       * tPRESC = (PRESC+1) x tI2CCLK
       * SDADEL >= {tf +tHD;DAT(min) - tAF(min) - tDNF - [3 x tI2CCLK]} / {tPRESC}
       * SDADEL <= {tVD;DAT(max) - tr - tAF(max) - tDNF- [4 x tI2CCLK]} / {tPRESC}
       */
      tsdadel_min = (int32_t)I2C_Charac[i2c_speed].tfall +
                    (int32_t)I2C_Charac[i2c_speed].hddat_min -
                    (int32_t)tafdel_min - (int32_t)(((int32_t)I2C_Charac[i2c_speed].dnf +
                                                     3) * (int32_t)ti2cclk);
      tsdadel_max = (int32_t)I2C_Charac[i2c_speed].vddat_max -
                    (int32_t)I2C_Charac[i2c_speed].trise -
                    (int32_t)tafdel_max - (int32_t)(((int32_t)I2C_Charac[i2c_speed].dnf +
                                                     4) * (int32_t)ti2cclk);
      /* {[tr+ tSU;DAT(min)] / [tPRESC]} - 1 <= SCLDEL */
      tscldel_min = (int32_t)I2C_Charac[i2c_speed].trise +
                    (int32_t)I2C_Charac[i2c_speed].sudat_min;
      if (tsdadel_min <= 0) {
        tsdadel_min = 0;
      }
      if (tsdadel_max <= 0) {
        tsdadel_max = 0;
      }

      /* tDNF = DNF x tI2CCLK */
      dnf_delay = I2C_Charac[i2c_speed].dnf * ti2cclk;

      clk_max = SEC2NSEC / I2C_Charac[i2c_speed].freq_min;
      clk_min = SEC2NSEC / I2C_Charac[i2c_speed].freq_max;

      prev_error = ti2cspeed;

      for (presc = 0; presc < I2C_PRESC_MAX; presc++) {
        for (scldel = 0; scldel < I2C_SCLDEL_MAX; scldel++) {
          /* TSCLDEL = (SCLDEL+1) * (PRESC+1) * TI2CCLK */
          uint32_t tscldel = (scldel + 1U) * (presc + 1U) * ti2cclk;
          if (tscldel >= (uint32_t)tscldel_min) {

            for (sdadel = 0; sdadel < I2C_SDADEL_MAX; sdadel++) {
              /* TSDADEL = SDADEL * (PRESC+1) * TI2CCLK */
              uint32_t tsdadel = (sdadel * (presc + 1U)) * ti2cclk;
              if ((tsdadel >= (uint32_t)tsdadel_min) && (tsdadel <=
                                                         (uint32_t)tsdadel_max)) {
                if (presc != prev_presc) {
                  valid_timing_nbr ++;
                  if (valid_timing_nbr >= I2C_VALID_TIMING_NBR) {
                    return ret;
                  }
                  /* tPRESC = (PRESC+1) x tI2CCLK*/
                  uint32_t tpresc = (presc + 1U) * ti2cclk;
                  for (scll = 0; scll < I2C_SCLL_MAX; scll++) {
                    /* tLOW(min) <= tAF(min) + tDNF + 2 x tI2CCLK + [(SCLL+1) x tPRESC ] */
                    uint32_t tscl_l = tafdel_min + dnf_delay + (2U * ti2cclk) + ((scll + 1U) * tpresc);
                    /* The I2CCLK period tI2CCLK must respect the following conditions:
                    tI2CCLK < (tLOW - tfilters) / 4 and tI2CCLK < tHIGH */
                    if ((tscl_l > I2C_Charac[i2c_speed].lscl_min) &&
                        (ti2cclk < ((tscl_l - tafdel_min - dnf_delay) / 4U))) {
                      for (sclh = 0; sclh < I2C_SCLH_MAX; sclh++) {
                        /* tHIGH(min) <= tAF(min) + tDNF + 2 x tI2CCLK + [(SCLH+1) x tPRESC] */
                        uint32_t tscl_h = tafdel_min + dnf_delay + (2U * ti2cclk) + ((sclh + 1U) * tpresc);
                        /* tSCL = tf + tLOW + tr + tHIGH */
                        uint32_t tscl = tscl_l + tscl_h + I2C_Charac[i2c_speed].trise +
                                        I2C_Charac[i2c_speed].tfall;
                        if ((tscl >= clk_min) && (tscl <= clk_max) &&
                            (tscl_h >= I2C_Charac[i2c_speed].hscl_min) && (ti2cclk < tscl_h)) {
                          int32_t error = (int32_t)tscl - (int32_t)ti2cspeed;
                          if (error < 0) {
                            error = -error;
                          }
                          /* look for the timings with the lowest clock error */
                          if ((uint32_t)error < prev_error) {
                            prev_error = (uint32_t)error;
                            ret = ((presc & 0x0FU) << 28) | \
                                  ((scldel & 0x0FU) << 20) | \
                                  ((sdadel & 0x0FU) << 16) | \
                                  ((sclh & 0xFFU) << 8) | \
                                  ((scll & 0xFFU) << 0);
                            prev_presc = presc;
                            /* Save I2C Timing found for further reuse (and avoid to compute again) */
                            I2C_ClockTiming[i2c_speed].timing = ret;
                            //printf("tsdadel = %i\n", tsdadel);
                            //printf("tscldel = %i\n", tscldel);
                        	printf("I2C configuration = %i\n", ret);
                         }
                        }
                      }
                    }
                  }
                }
              }
            }
          }
        }
      }
    }
  }
  return ret;
}

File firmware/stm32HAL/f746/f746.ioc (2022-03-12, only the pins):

Mcu.UserName=STM32F746ZGTx
PA0/WKUP.GPIO_Label=L_MOTOR_PWM
PA0/WKUP.Signal=S_TIM2_CH1_ETR
PA1.GPIO_Label=RMII_REF_CLK [LAN8742A-CZ-TR_REFCLK0]
PA1.Signal=ETH_REF_CLK
PA10.GPIO_Label=USB_ID
PA10.Signal=USB_OTG_FS_ID
PA11.GPIO_Label=USB_DM
PA11.Signal=USB_OTG_FS_DM
PA12.GPIO_Label=USB_DP
PA12.Signal=USB_OTG_FS_DP
PA13.GPIO_Label=TMS
PA13.Signal=SYS_JTMS-SWDIO
PA14.GPIO_Label=TCK
PA14.Signal=SYS_JTCK-SWCLK
PA2.GPIO_Label=RMII_MDIO [LAN8742A-CZ-TR_MDIO]
PA2.Signal=ETH_MDIO
PA6.GPIO_Label=R_ENC_CH1
PA6.Signal=S_TIM3_CH1
PA7.GPIO_Label=RMII_CRS_DV [LAN8742A-CZ-TR_CRS_DV]
PA7.Signal=ETH_CRS_DV
PA8.GPIO_Label=USB_SOF [TP1]
PA8.Signal=USB_OTG_FS_SOF
PA9.GPIO_Label=USB_VBUS
PA9.Signal=USB_OTG_FS_VBUS
PB0.GPIO_Label=LD1 [Green]
PB0.Signal=GPIO_Output
PB13.GPIO_Label=RMII_TXD1 [LAN8742A-CZ-TR_TXD1]
PB13.Signal=ETH_TXD1
PB14.GPIO_Label=LD3 [Red]
PB14.Signal=GPIO_Output
PB3.GPIO_Label=SW0
PB3.Signal=SYS_JTDO-SWO
PB7.GPIO_Label=LD2 [Blue]
PB7.Signal=GPIO_Output
PB8.GPIO_Label=IMU_SCL
PB8.Signal=I2C1_SCL
PB9.GPIO_Label=IMU_SDA
PB9.Signal=I2C1_SDA
PC1.GPIO_Label=RMII_MDC [LAN8742A-CZ-TR_MDC]
PC1.Signal=ETH_MDC
PC13.GPIO_Label=USER_Btn [B1]
PC13.Signal=GPXTI13
PC14/OSC32_IN.Signal=RCC_OSC32_IN
PC15/OSC32_OUT.Signal=RCC_OSC32_OUT
PC4.GPIO_Label=RMII_RXD0 [LAN8742A-CZ-TR_RXD0]
PC4.Signal=ETH_RXD0
PC5.GPIO_Label=RMII_RXD1 [LAN8742A-CZ-TR_RXD1]
PC5.Signal=ETH_RXD1
PC7.GPIO_Label=R_INC_CH2
PC7.Signal=S_TIM3_CH2
PD12.GPIO_Label=L_ENC_CH1
PD12.Signal=S_TIM4_CH1
PD13.GPIO_Label=L_ENC_CH2
PD13.Signal=S_TIM4_CH2
PD8.GPIO_Label=STLK_RX [STM32F103CBT6_PA3]
PD8.Signal=USART3_TX
PD9.GPIO_Label=STLK_TX [STM32F103CBT6_PA2]
PD9.Signal=USART3_RX
PE11.GPIO_Label=R_MOTOR_DIR
PE11.Signal=GPIO_Output
PE9.GPIO_Label=R_MOTOR_PWM
PE9.Signal=S_TIM1_CH1
PF14.GPIO_Label=L_MOTOR_DIR
PF14.Signal=GPIO_Output
PF15.GPIO_Label=IMU_INT
PF15.Signal=GPXTI15
PG11.GPIO_Label=RMII_TX_EN [LAN8742A-CZ-TR_TXEN]
PG11.Signal=ETH_TX_EN
PG13.GPIO_Label=RMII_TXD0 [LAN8742A-CZ-TR_TXD0]
PG13.Signal=ETH_TXD0
PG6.GPIO_Label=USB_PowerSwitchOn [STMPS2151STR_EN]
PG6.Signal=GPIO_Output
PG7.GPIO_Label=USB_OverCurrent [STMPS2151STR_FAULT]
PG7.Signal=GPIO_Input
PH0/OSC_IN.GPIO_Label=MCO [STM32F103CBT6_PA8]
PH0/OSC_IN.Signal=RCC_OSC_IN
PH1/OSC_OUT.Signal=RCC_OSC_OUT

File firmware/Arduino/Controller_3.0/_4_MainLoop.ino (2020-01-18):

void loop() {

  if (Serial.available() > 0) {
    stat = Serial.read();
  }


  // Main State Machine, dictated by user's input through serial monitor
  switch (stat) {

    // MODE - Main Loop, enters if either charging or balancing
    case  127:
    case 121:
    case 104:
    case 110:
    case 117:
    case 106:
    case 109:

      p = 0;                                        // If switching to balanceing, reset integrals
      if (stat == 117 || stat == 106 || stat == 109) {
        p = 1;
      }

      get_IMU_Values();
      get_left_Encoder_Speeds();
      get_right_Encoder_Speeds();
      
      get_left_PID_Voltage_Value ();
      get_right_PID_Voltage_Value ();

      switch (stat) {
        case 121:                                     // y - Charge left motor
          left_Voltage = left_Target_Voltage;
          right_Voltage = 0;
          break;

        case 104:                                     // h - Charge right motor
          left_Voltage = 0;
          right_Voltage = right_Target_Voltage;
          break;

        case 110:                                     // n - Charge both motors
          left_Voltage = left_Target_Voltage;
          right_Voltage = right_Target_Voltage;
          break;

        case 117:                                     // u - Balnce with left motor
          left_Voltage = left_PID_Voltage;
          right_Voltage = 0;
          break;

        case 106:                                     // j - Balance with right motor
          left_Voltage = 0;
          right_Voltage = right_PID_Voltage;
          break;

        case 109:                                     // m - Balance with both motors
          left_Voltage = left_PID_Voltage;
          right_Voltage = right_PID_Voltage;
          break;

        default:                                      // space - Motors off, but print updates
          left_Voltage = 0;
          right_Voltage = 0;
          break;
      }


      set_left_Motor_Voltage();
      set_right_Motor_Voltage();



      //////////////////////////////////////////// START SERIAL PRINT///////////////////////////////////////////////////////////////
      //////////////////////////////////////////////////////////////////////////////////////////////////////////////////////////////

      // Serial Console
      package = "";
      time_Probe_Prev = micros();
      //    Serial.print(l);
      //    Serial.print("\t");


      //       Serial.print((int)hertz);
      //       Serial.print("\t");
      package += millis();
      package += "\t";
      ////      Serial.print("PID:\t");
      ////      Serial.print(int(theta_Kp));
      ////      Serial.print("\t");
      ////      Serial.print(int(theta_Ki));
      ////      Serial.print("\t");
      ////      Serial.print(int(theta_Kd));
      //      Serial.print("\t");


      //      Serial.print(F("Speed|Accel:")); undo
      //      Serial.print("\t");
      //
      //      //    Serial.print(left_Time_Age);
      //      //    Serial.print("\t");
      //      //    Serial.print(left_Time_Saved);
      //      //    Serial.print("\t");
      package += "\t";
//      package += (int)left_Abs_Tick_Count;
//      package += "\t\t";
      package += (int)left_Speed_RPM;
      package += "\t";
//      package += (int)left_Speed_RPM_Unfiltered;
//      package += "\t";
      package += (int)right_Speed_RPM;
      package += "\t";
//      package += left_Encoder_Direction_Debug * 100;
//      package += "\t";
      //      Serial.print((int)left_Acceleration);
      //      Serial.print("\t");
      //      Serial.print((int)right_Acceleration);
      //      Serial.print("\t");
      //    Serial.print(left_Voltage);
      //    Serial.print("\t");
      //    Serial.print("\t");

      //    Serial.print(left_Voltage);
      //    Serial.print("\t");
      //    Serial.print(right_Voltage);
      //    Serial.print("\t");
      //    Serial.print("\t");
      //
      //      Serial.print("Pos:\t"); undu
      //      Serial.print(theta_Error);
      //      Serial.print("\t");
      //      Serial.print(omega_Error);
      //      Serial.print("\t");
      //      Serial.print("\t");
      //
      //    Serial.print("Wheel Speed:\t");
      //    Serial.print((int)left_Speed_RPM);
      //    Serial.print("\t");
      //    Serial.print(int(right_Speed_RPM));
      //    Serial.print("\t");
      //    Serial.print("\t");
      //        Serial.print(left_Time_Prev);
      //        Serial.print("\t");
      //        Serial.print(left_Time_Now);
      //        Serial.print("\t");
      //    Serial.print(left_Encoder_Direction);
      //    Serial.print("\t");
      //    Serial.print(encoder_Resolution_Size);
      //    Serial.print("\t");

      //    Serial.print("Wheel Acc.:\t");
      //    Serial.print((int)left_Acceleration);
      //    Serial.print("\t");

      //    Serial.print("YPR:\t");
      //    Serial.print(ypr[0] * 180 / M_PI);
      //    Serial.print("\t");
      //    Serial.print(ypr[1] * 180 / M_PI);
      //    Serial.print("\t");
      //    Serial.print(ypr[2] * 180 / M_PI);
      //    Serial.print("\t");
      //    Serial.print("\t");

      //    Serial.print("Theta Error:\t");
      //    Serial.print(theta_Error);
      //    Serial.print("\t");
      //    Serial.print("\t");

      //    Serial.print("Theta Speed:\t");
      //    Serial.print(theta_Speed_Now);
      //    Serial.print("\t");
      //    Serial.print("\t");
      //
      //    Serial.print("Theta Integra;:\t");
      //    Serial.print(theta_Integral);
      //    Serial.print("\t");
      //    Serial.print("\t");

      //    Serial.print("Wheel Pos:\t");
      //    Serial.print(left_Abs_Tick_Count);
      //    Serial.print("\t");
      //    Serial.print(right_Abs_Tick_Count);
      //    Serial.print("\t");
      //    Serial.print("\t");

      //      Serial.print(F("CurrentMax|Avg:\t"));
      //      Serial.print(left_Current_Max);
      //      Serial.print("\t");
      //      //    //    Serial.print(right_Current_Max);
      //      //    //    Serial.print("\t");
      //      //    Serial.print("\t");
      //      //
      //      //    Serial.print("CurrentAvg:\t");
      //      Serial.print(left_Current_Avg);
      //      Serial.print("\t");
      //      //    Serial.print(right_Current_Avg);
      //      //    Serial.print("\t");
      //      Serial.print("\t");

      //    Serial.print("PID:\t");
      //    Serial.print(int(theta_Kp));
      //    Serial.print("\t");
      //    Serial.print(int(theta_Ki));
      //    Serial.print("\t");
      //    Serial.print(int(theta_Kd));
      //    Serial.print("\t");
      //    Serial.print("\t");
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

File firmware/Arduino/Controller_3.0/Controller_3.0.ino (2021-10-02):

//////////////////////////////////////////////
// file: Controller_3.0.ino
//////////////////////////////////////////////

// Library Inclusions

#include <I2Cdev.h>                             // IMU IC2 Communication
#include <Wire.h>                               // IMU IC2 Communication
#include "MPU6050_6Axis_MotionApps20_mod_1.h"   // IMU,  changed value in line 305 to 1 to change update speed from every 15ms to every 10ms
#include <PinChangeInt.h>                       // Pin Change Interrupt
#include <digitalWriteFast.h>                   // Fast Digital Readings

// #define CUSTOM
#define POLOLU

#if defined(CUSTOM)
  // PinAssignments
  // These pin assignments correspond to the Arduino shield developed as part of this project.
  
  #define   pin_left_PMW          7    // PWM output for Left Motor
  #define   pin_left_EncoderB     A2   // Encoder_B input from Left Motor
  #define   pin_left_dir          8
  
  #define   pin_right_PMW         12   // PWM output for Left Motor
  #define   pin_right_EncoderB    6    // Encoder_B input from Right Moor
  #define   pin_right_dir         13
  
  #define   pin_IMU_Interrupt     A3
  #define   pin_IMU_SDA           A4
  #define   pin_IMU_SCL           A5
  
  // Interrupt Assignment
  
  #define   interruptPin_left_Encoder    0   // mapped to D2 - pin_left_EncoderA
  #define   interruptPin_right_Encoder   1   // mapped to D3 - pin_right_EncoderA
#else
  #if defined(POLOLU)
    // PinAssignments
    // These pin assignments correspond to the Pololu Dual MAX14870 Motor Driver Shield for Arduino.
    // https://www.pololu.com/product/2519
    
    #define   pin_left_PMW          9    // PWM output for Left Motor
    #define   pin_left_EncoderB     A2   // Encoder_B input from Left Motor
    #define   pin_left_dir          7
    
    #define   pin_right_PMW         10   // PWM output for Left Motor
    #define   pin_right_EncoderB    6    // Encoder_B input from Right Moor
    #define   pin_right_dir         8
    
    #define   pin_IMU_Interrupt     A3
    #define   pin_IMU_SDA           A4
    #define   pin_IMU_SCL           A5
    
    // Interrupt Assignment
    
    #define   interruptPin_left_Encoder    0   // mapped to D2 - pin_left_EncoderA
    #define   interruptPin_right_Encoder   1   // mapped to D3 - pin_right_EncoderA
  #endif
#endif

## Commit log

2017-10-16 added 3d print files, references, modified reaction wheel to match pololu hubs and motors
    [25d-gearmotor-4.4-9.7.step, 25d-metal-gearmotor-172-227-encoder.step, 25d-metal-gearmotor-172-227.step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]
2017-10-29 added nucleo references
    [MB1180.PcbDoc, MB1180.PcbLib, MB1180.PrjPCB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]
2019-04-01 updated readme to begin documenting current design
2019-04-02 big catch-up commit
    [motorConstant.xlsx, motorResistance.xlsx, speed test.xlsx]
2019-04-03 cleaning up file structure
    [centerBlock.stl, motorClip.stl, motorConstant.xlsx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]
2019-04-04 first cut at Arduino software
2019-04-05 rearrange harware files and add drawing of simple reaction wheel
    [centerBlock.stl, motorClip.stl, topBlock.stl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]
2019-04-07 updated drawing of simplified reaction wheel
2019-04-29 updated motor mount clip drawing
2019-04-30 added fabrication notes for the motor mounting clip
2019-05-01 added svg of motor mount clip used for x-carve
2019-11-20 wiring schematic added and arduino software updated with pin definitions to match
    [balancing_stick_schematic.kicad_pcb, balancing_stick_schematic.sch]
2020-01-18 update Arduino software to use a motor driver based on the MAX14870 IC
2020-01-18 add KICAD design for the motor controller and gyro shield
    [BOM.xlsx, balancing_stick_schematic.kicad_pcb, balancing_stick_schematic.sch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]
2020-01-20 corrected pin definitions for the Pololu Dual MAX14870 motor driver shield
    [Controller_3.0.ino]
2020-01-20 updated schematic pdf and generated gerber files
    [motor_controller-B_Cu.gbl, motor_controller-B_Mask.gbs, motor_controller-B_Paste.gbp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]
2020-01-27 added some documentation and updated some values to match the Pololu motors
2020-01-30 updated IMU offsets to reflect measured values from the calibrateIMU sketch
2020-01-30 corrected the encoder_PPR constant from 12 to 52.8 to reflect the 4.4:1 gear ratio
    [_1_Global_Variables.ino]
2020-01-30 rearranged folders, removed cruft, and updated README files
    [MB1180.PcbDoc, MB1180.PcbLib, MB1180.PrjPCB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]
2020-01-31 improved dimension callouts for gyro mounting block drawing
2020-02-07 fully functioning encoder test sketch #2
2021-10-02 updating to reflect as-built design
    [BOM.ods, BOM.xlsx]
2021-10-02 updating the structure of the folders
    [motor_controller-B_Cu.gbl, motor_controller-B_Mask.gbs, motor_controller-B_Paste.gbp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]
2021-10-02 update schematic for newer version of Kicad
    [motor_controller.sch]
2021-10-08 first cut at STM#@ firmware
2021-10-10 create an stm32f746 version with more ram
2021-10-14 correct the LED port and pin
2021-10-14 Add a readme for the STM32 firmware
2021-10-14 create LED class and an enum for return codes
2021-10-16 add terminal commands and fix printf usage
    [commands.cpp]
2021-10-19 ensure Nodate's printf routine is used rather than stdlib
2021-10-23 Initial cut at mpu6050 interface
2021-10-31 imu, mpu6050 and I2Cdev compile
2021-11-02 initial motor and encoder classes
2021-11-17 fleshed out files and corrected compilation bugs
    [imu.cpp, motor.cpp]
2021-12-03 first commit of STM32 HAL version of firmware (work in progress)
2021-12-04 Add interrupt service for Timer1 and and a Timer1 filter
2021-12-05 shuffle timers, add a microsec clock, and flesh out the encoder
2021-12-08 converting project to C++ to support using the IMU code
2021-12-08 more i2cdev and mpu6050 changes to accommodate STM32 HAL
2021-12-09 converted motor functions to a Motor class
2021-12-09 added encoder and imu status returns
2021-12-11 limit motor pwm to <50kHz
2021-12-11 correct the encoder counts per rev
    [encoder.hpp]
2021-12-11 set the I2c rise and fall times to non-zero values
2021-12-14 Changed I2C1 SCL from PB6 to PB8
2021-12-16 correct I2Cdev HAL interface and up the uart speed
    [f746.ioc, imu.cpp]
2021-12-17 swap pins to be consistent with Arduino Uno for imu interrupt
    [f746.ioc, main.h]
2021-12-18 annotate the imu class
2021-12-25 utility to calculate stm32 I2C timing register value
2021-12-29 functional polling version with initial reset
    [main.c, main.h]
2021-12-29 remove debug statements from I2Cdev.c
2021-12-30 working set of accel and gyro offsets
2022-01-07 fix big/little endian issues and add return code testing
    [appEntry.cpp]
2022-01-09 functioning basic gyro and accelerometer testing
2022-01-19 update STM32CUBEIDE to 1.8.0, changing generated files
2022-01-21 functional interrupt-driven dmp test
2022-01-29 add imu to the command list
2022-01-29 broken, but working on it
    [appEntry.cpp, commands.cpp, encoder.hpp]
2022-02-12 clean up the introduction of rotor velocity feedback
2022-02-12 add a matlab flag to determine regular or simple rotor parameters
2022-02-19 fixed gear ratio discussion, shaft work, and implementation details
2022-02-20 improved method for determining motor constants
2022-02-24 updated measured motor data
2022-02-24 change TODO to FIXME, improving task sorting in IDE
    [controller.cpp, encoder.cpp, imu.cpp]
2022-03-02 add digital filter class
2022-03-02 modify imu class to use filter class
2022-03-03 sort out true, false, error definition conflicts
    [appEntry.cpp, imu.cpp, serial.c]
2022-03-03 refactored use of theta/omega in imu methods
2022-03-09 move calculation of the integral of angle error to the controller
    [appEntry.cpp, controller.cpp, imu.cpp]
2022-03-10 move angle_Zero calculation to controller class
    Moved the calculation of the reference (or zero) angle from the imu class to the controller class.
2022-03-12 correct the TIMER 5 prescaler to reflect a 1 usec counter
    [f746.ioc, main.c]
2022-03-13 update description of motor constant measurement
    [data.xlsx, motorConstant.xlsx, motorResistance.xlsx]
2022-07-24 Added acrylic reaction wheel design
    [acrylic disk.xlsx, steel disk.xlsx]
2023-06-06 add button to control changing target voltages
